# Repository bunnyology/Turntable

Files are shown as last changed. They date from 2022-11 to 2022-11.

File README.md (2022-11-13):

# Arduino controlled turntable

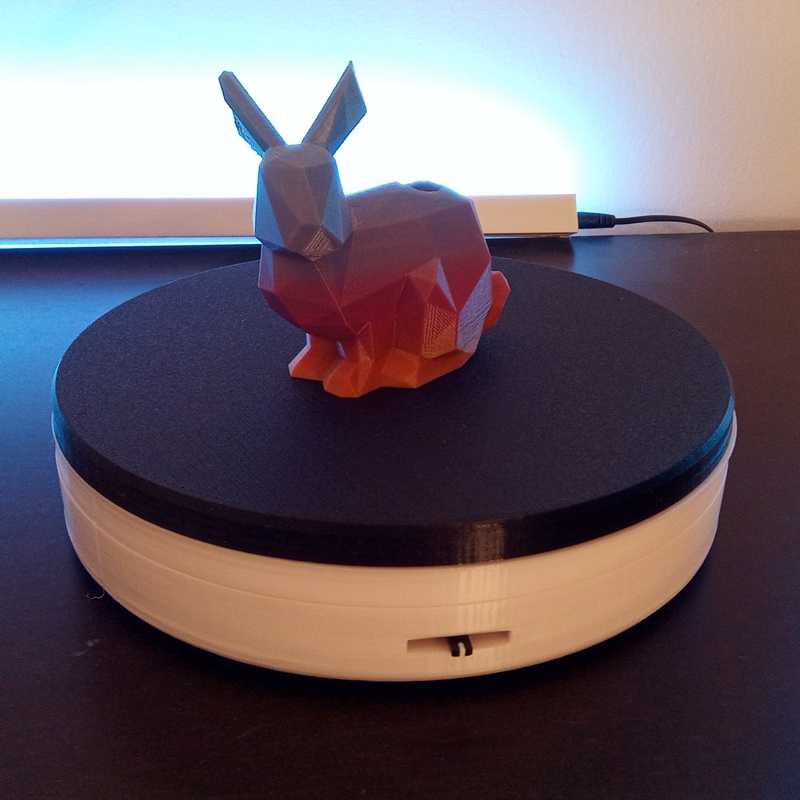
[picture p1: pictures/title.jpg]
Turntable


Some time ago, I got a 3D scanner from a kickstarter campaign and needed now a turntable for scanning objects. 

I had some cheap, unused 28-BJY stepper motors available. On the paper they seemed to be perfectly suitable for a turntable. They feature a 1:64 gearing mechanism, which should apply enough strengh for turning small object, and its maximum speed of about 3-4 seconds per full revolution is more than enough.

As I wasn't sure, how fast the object may or must be moved for scanning, I wanted to adjust the rotation speed later. So, the speed can be adjusted by a sliding potentiometer.

## Required parts

- 1 pc. Arduino nano
- 1 pc. stepper motor 28-BYJ-48 with ULN2003 driver board (available for about 3 Euro in sets of 5)
- 1 pc. linear/sliding potentiometer (50kOhm, 25 mm sliding path, available for about 2 Euro in sets of 10)
- 6 pcs. 6mm steel balls
- 2 pcs. M4x12 screws and nuts for mounting the stepper motor
- 3 pcs. M3x20 screws and
- 3 pcs. M3 threaded insets for assembling the base
## Wiring

Wiring is rather simple: The ULN2003 driver board (IN1..IN4) is connected to the Arduino GPIOs D8..D11. The middle pin of the potentiometer is connected to A0. Use GND and 5V pins as power source for both components.

## Printing

I've printed all parts in PLA with a 0.6mm nozzle and 0.28mm layer height to save time (overall printing time was about 9 hours). A standard 0.4mm nozzle and a 0.2mm layer height might probably lead to better tolerances and smoother operation.

However, the groves and particularily the bearing washer needs to be sanded, so that the touching surfaces can slide well.

All parts can be printed without supports.

## Software

Use the attached Arduino sketch to run the turntable. 

To exploit the full potential of the stepper motor, half step driving is used to controlthe motor. The potentiometer setting is converted into a time delay between the steps. 

A lever position in the middle will completely power off the motor. Sliding the lever to the right turns the plate clockwise, sliding to the left turns the plate counter-clockwise.

## Remarks regarding the design

I didn't want to use large, expensive ball bearings, so I simply used a few 6mm steel balls running in a circular groove to maintain the distance between turning plate and base, even when there is a excentric weight on the turning plate. I had to learn, that filling this groove completely with steel balls excerted just too much friction. The less balls I used, the better the turntable worked. So, finally, I designed a ball bearing spacer to keep six balls at constant distance.

I must admit, that the 23-BYJ stepper motor is too week for really smooth operation. It is powered by the 5V USB supply and draws about 250mA. I'll probably redesign the turntable using a proper motor or mod the motor and use it with a full H bridge in bipolar mode- but that would require a more sophisticated power supply, and additional complexity. However, I had these cheap stepper motors laying around, anyway, and it is sufficiently working for my intended purpose.

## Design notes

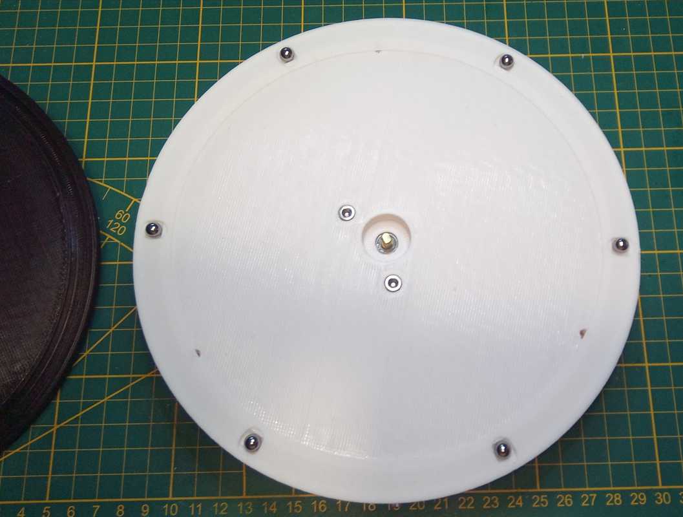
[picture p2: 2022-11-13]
pictures/bottom+bearings.jpg

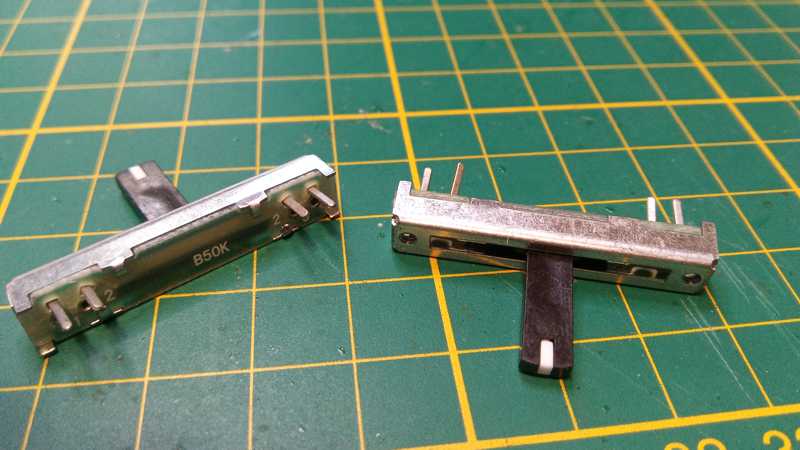
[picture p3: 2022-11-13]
pictures/poti.jpg

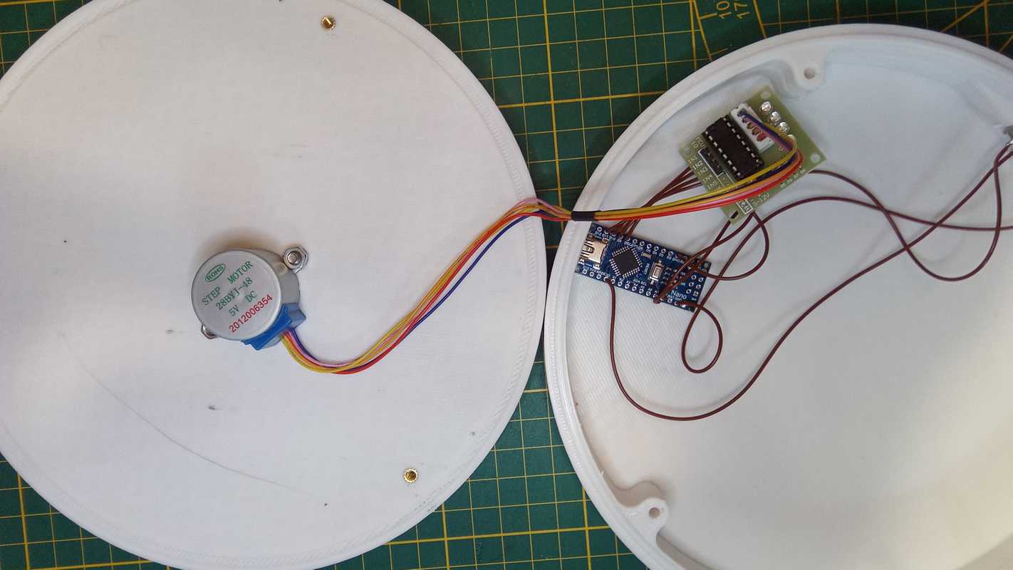
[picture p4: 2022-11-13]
pictures/stepper-mount.jpg

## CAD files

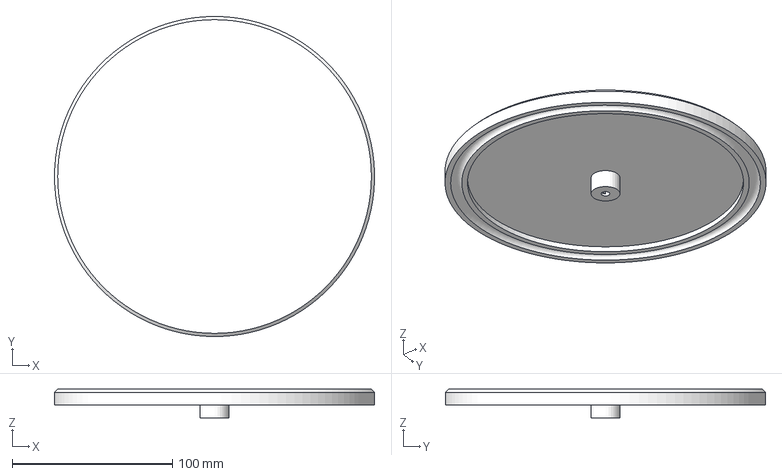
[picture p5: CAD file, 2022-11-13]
3Dmodel/Turntable-top.3mf
200.0 x 200.0 x 18.0 mm

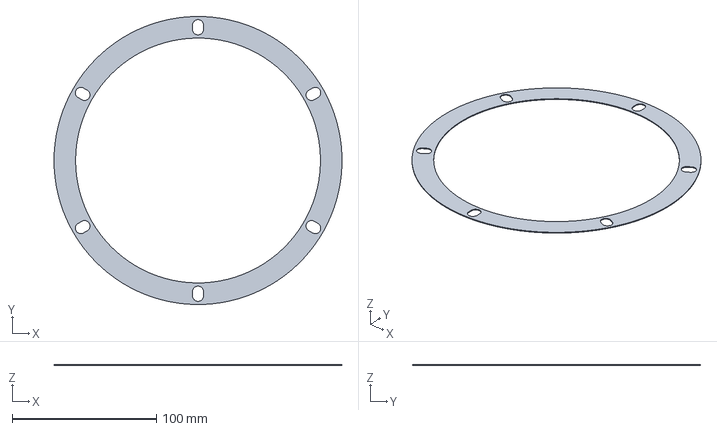
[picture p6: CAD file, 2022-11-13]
3Dmodel/Turntable-bearing.3mf
200.0 x 200.0 x 0.6 mm

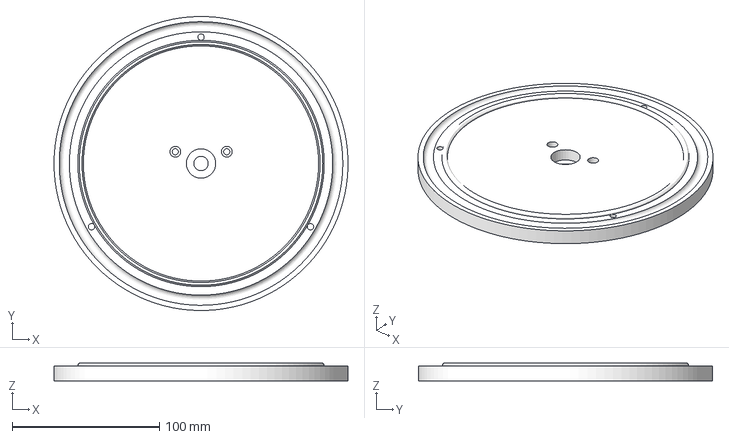
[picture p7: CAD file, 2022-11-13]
3Dmodel/Turntable-mid.3mf
200.0 x 200.0 x 12.0 mm

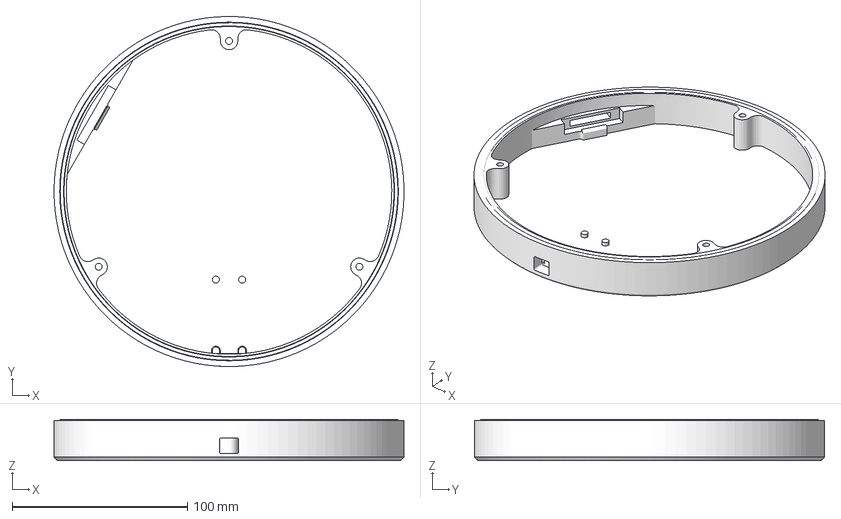
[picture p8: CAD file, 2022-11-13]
3Dmodel/Turntable-bottom.3mf
200.0 x 200.0 x 23.6 mm

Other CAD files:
3Dmodel/Turntable v8.f3d

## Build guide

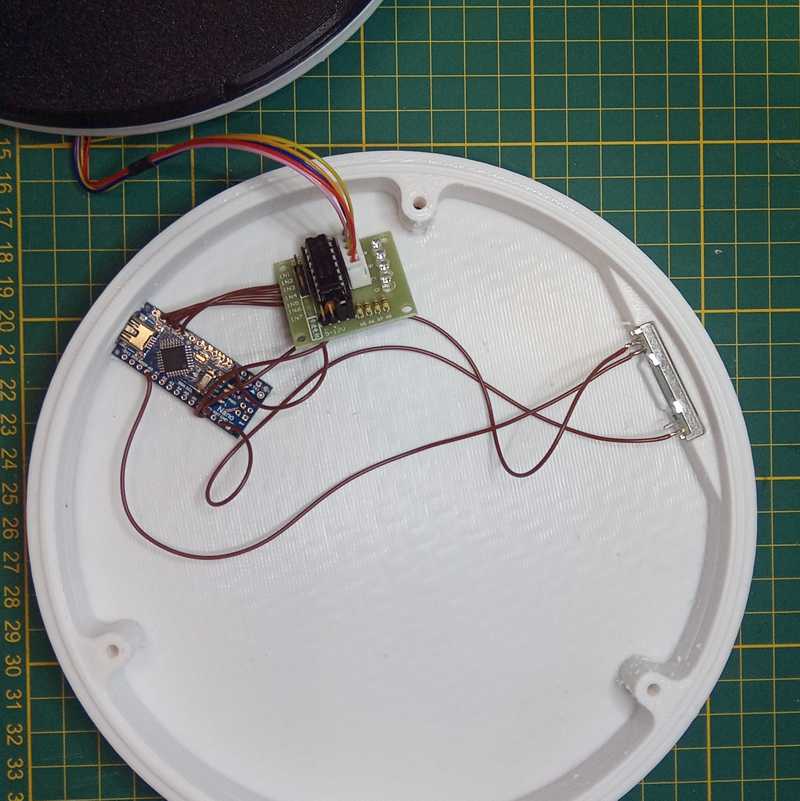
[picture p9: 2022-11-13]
pictures/wiring.jpg

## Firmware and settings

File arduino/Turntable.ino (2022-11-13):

/*
** Turntable control
** (C) Copyright 2022 by bunnyology
** https://github.com/bunnyology/Turntable.git
** --------------------------------------------------------
** Monophasic stepper motor 28-BYJ-48 with ULN2003
** driver (4 channels). 8 half steps.
** Wiring:
**   GPIO    MOTOR  ULN2003
**    D8  ->   B'    (IN1)
**    D9  ->   A     (IN2)
**    D10 ->   B     (IN3)
**    D11 ->   A'    (IN4)
**
** Linear/sliding potentiometer to control the speed
** connected to A0.
**
*/
#define STEPPER_MASK B11110000
#define STEPPER_STEPS 8

byte stepPattern[] = { 
  B00001000, 
  B00001100, 
  B00000100, 
  B00000110, 
  B00000010, 
  B00000011, 
  B00000001, 
  B00001001 
};
int step = 0;


void setup() {
  // analog input A0 to read potentiometer
  pinMode(A0, INPUT);
  // D8..D11 : OUTPUT
  DDRB = B00001111;
  PORTB = ( PORTB & STEPPER_MASK );   // all off
}

void loop() {
  // read potentiometer (10 bit -> 0...1023)
  int n = analogRead(A0);
  int dir;
  if( n < 512 ) {
    // slider on the left -> counter-clockwise
    dir = -1;
    n = 511 - n;
  } else {
    // slider on the right -> clockwise
    dir = 1;
    n -= 512;
  }
  
  // convert reading into number between 0..10
  int spd = n/48;
  if( spd == 0 ) {
    // lever in the middle -> power off
    PORTB = ( PORTB & STEPPER_MASK );   // all off
    delay(100);
    
  } else {
    // set stepper pattern according to current step
    PORTB = ( PORTB & STEPPER_MASK ) | stepPattern[step];
    
    // prepare next step
    step += dir;
    if( step < 0 ) step = STEPPER_STEPS;
    else if( step >= STEPPER_STEPS ) step = 0;
    
    // delay stepping according to potentiometer setting
    // between 12000 us (slow) and 1200 us (fast)
    delayMicroseconds(12000 / spd);
  }
}
